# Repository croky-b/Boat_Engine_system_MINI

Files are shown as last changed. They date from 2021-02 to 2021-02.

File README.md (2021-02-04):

# Boat_Engine_system_MINI
Adaptation du projet de :https://github.com/TheDIYGuy999/Rc_Engine_Sound_ESP32 pour une utilisation "bateau"

Errata : Board Ver 1.6 : ESC1 et Led  4 partage la même Pin 19 

Il est possible de couper la piste en arriere de la resistance R10 et de relier un cable de R10 à D15 

une Nouvelle version 1.7 serra uploader

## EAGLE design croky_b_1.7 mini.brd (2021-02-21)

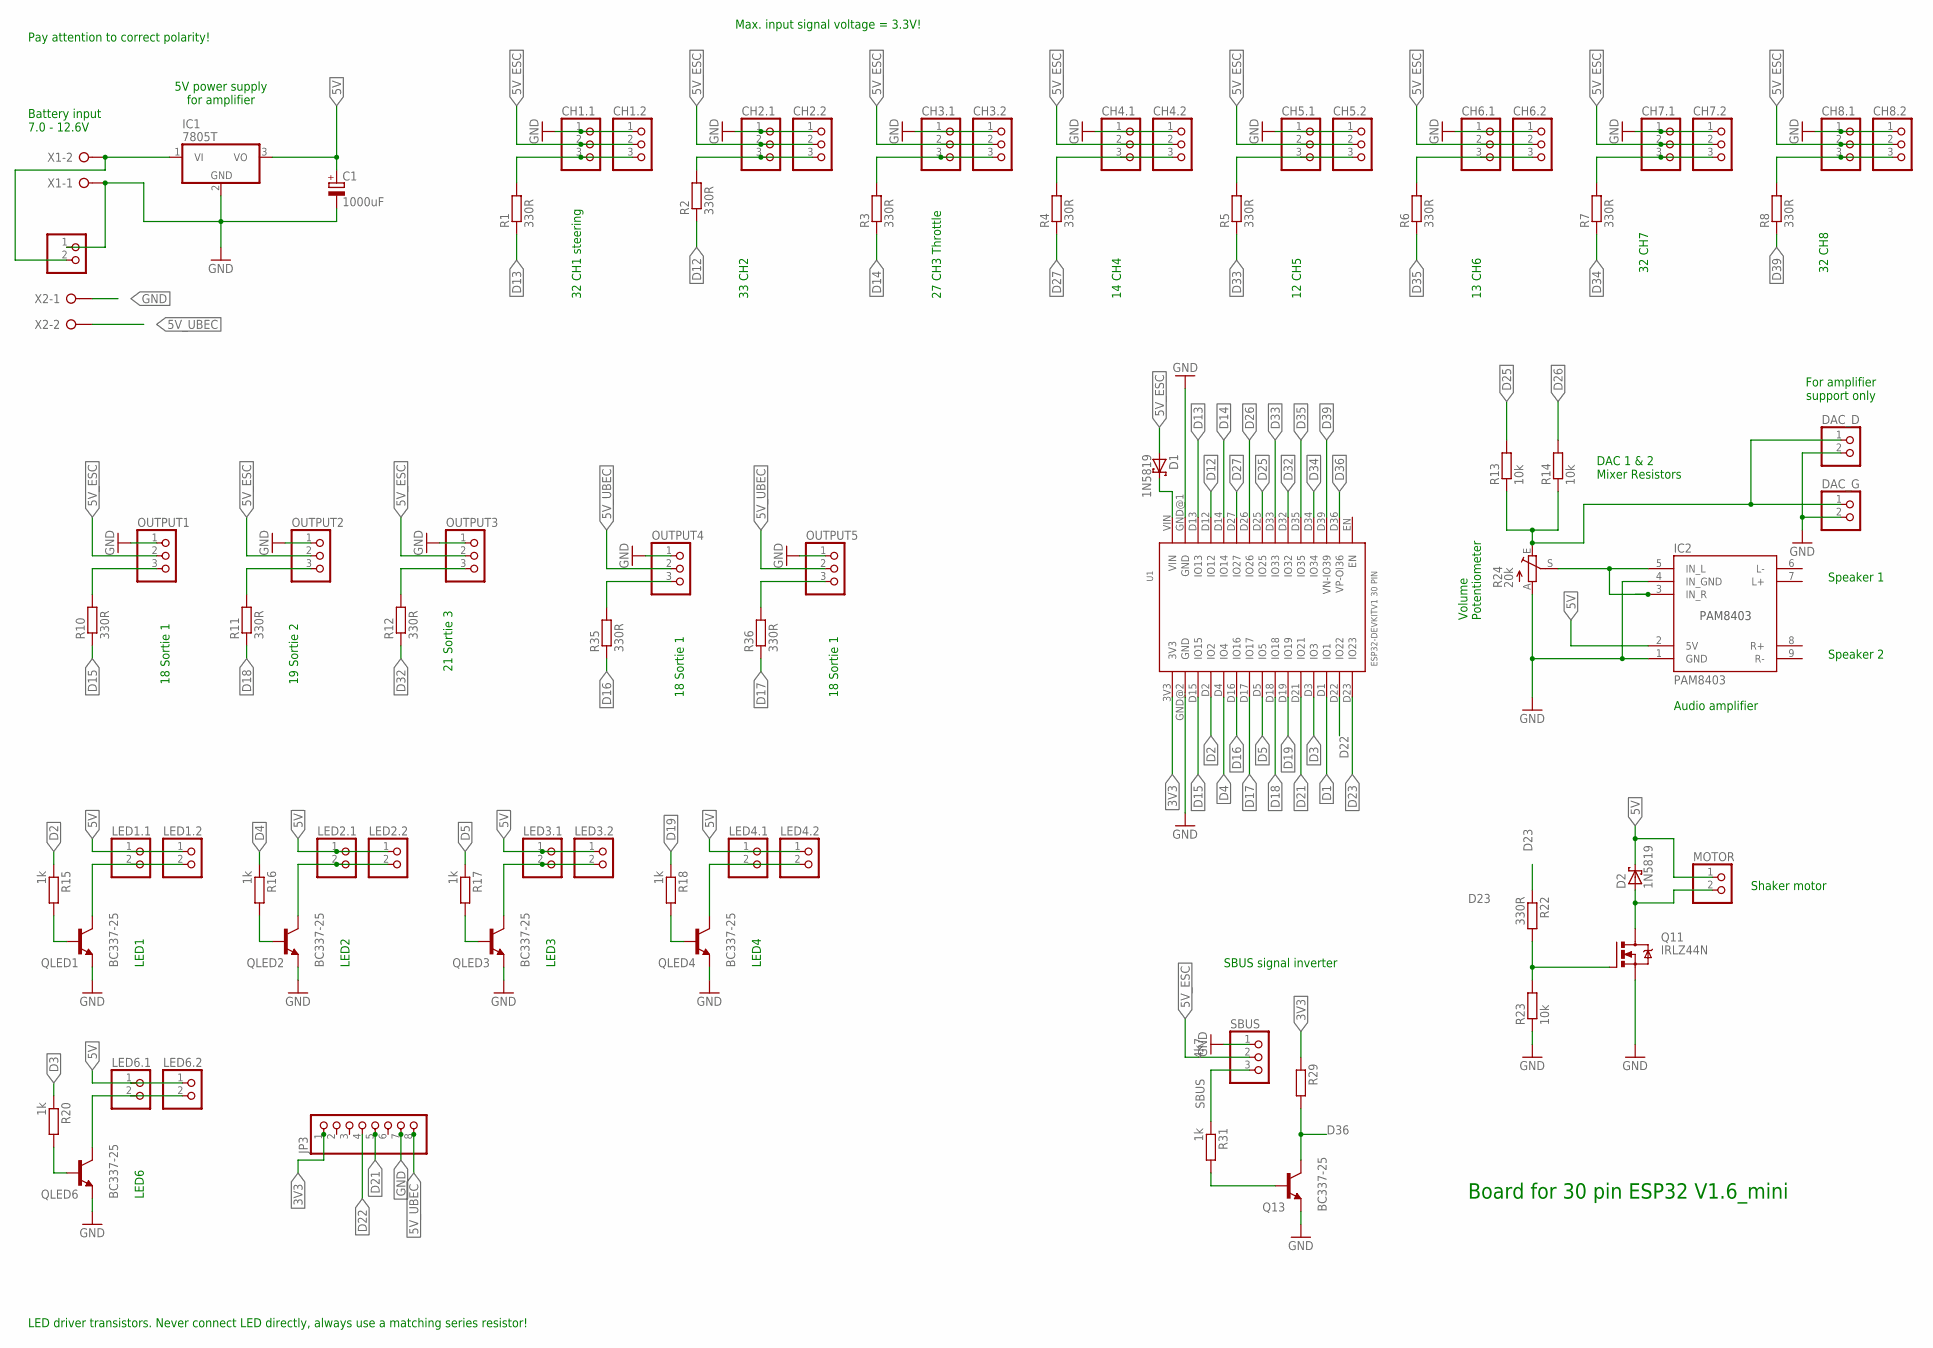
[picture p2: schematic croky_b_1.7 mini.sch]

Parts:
C1: 1000uF; E5-10,5
CH1.1, CH1.2, CH2.1, CH2.2, CH3.1, CH3.2, CH4.1, CH4.2, CH5.1, CH5.2, CH6.1, CH6.2, CH7.1, CH7.2, CH8.1, CH8.2: PINHD-1X3; 1X03
D1, D2: 1N5819; DO35-7
DAC_D: PINHD-1X2; 1X02
DAC_G: PINHD-1X2; 1X02
IC1: 7805T; TO220H
IC2: PAM8403
JP3: PINHD-1X8; 1X08
LED1.1, LED1.2, LED2.1, LED2.2, LED3.1, LED3.2, LED4.1, LED4.2, LED6.1, LED6.2: PINHD-1X2; 1X02
MOTOR, MOTOR2: PINHD-1X2; 1X02
OUTPUT1, OUTPUT2, OUTPUT3, OUTPUT4, OUTPUT5: PINHD-1X3; 1X03
Q11: IRLZ44N; TO220BV
Q13: BC337-25; TO92
QLED1, QLED2, QLED3, QLED4, QLED6: BC337-25; TO92
R1, R2, R3, R4, R5, R6, R7, R8, R10, R11, R12, R22, R35, R36: 330R; 0207/2V
R13, R14: 10k; 0207/10
R15, R16, R17, R18, R20, R31: 1k; 0207/2V
R23: 10k; 0207/2V
R24: 20k; S64W
R29: 4k7; 0207/2V
SBUS: PINHD-1X3; 1X03
U1: ESP32DEVKITV1; ESP32-DEVKITV1
X1, X2: W237-02P; W237-132

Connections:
3V3: JP3.1, R29.1, U1.3V3
5V: C1.+, D2.C, IC1.3 (VO), IC2.2 (5V), LED1.1.1, LED1.2.1, LED2.1.1, LED2.2.1, LED3.1.1, LED3.2.1, LED4.1.1, LED4.2.1, LED6.1.1, LED6.2.1, MOTOR.1
5V_ESC: CH1.1.2, CH1.2.2, CH2.1.2, CH2.2.2, CH3.1.2, CH3.2.2, CH4.1.2, CH4.2.2, CH5.1.2, CH5.2.2, CH6.1.2, CH6.2.2, CH7.1.2, CH7.2.2, CH8.1.2, CH8.2.2, D1.A, OUTPUT1.2, OUTPUT2.2, OUTPUT3.2, SBUS.2
5V_UBEC: JP3.8, OUTPUT4.2, OUTPUT5.2, X2.2
-: LED2.1.2, LED2.2.2, QLED2.3 (C)
--: LED3.1.2, LED3.2.2, QLED3.3 (C)
BAT+: IC1.1 (VI), MOTOR2.2, X1.2
D1: U1.D1 (IO1)
D2: R15.1, U1.D2 (IO2)
D3: R20.1, U1.D3 (IO3)
D4: R16.1, U1.D4 (IO4)
D5: R17.1, U1.D5 (IO5)
D12: R2.1, U1.D12 (IO12)
D13: R1.1, U1.D13 (IO13)
D14: R3.1, U1.D14 (IO14)
D15: R10.1, U1.D15 (IO15)
D16: R35.1, U1.D16 (IO16)
D17: R36.1, U1.D17 (IO17)
D18: R11.1, U1.D18 (IO18)
D19: R18.1, U1.D19 (IO19)
D21: JP3.5, U1.D21 (IO21)
D22: JP3.4, U1.D22 (IO22)
D23: R22.1, U1.D23 (IO23)
D25: R13.2, U1.D25 (IO25)
D26: R14.2, U1.D26 (IO26)
D27: R4.1, U1.D27 (IO27)
D32: R12.1, U1.D32 (IO32)
D33: R5.1, U1.D33 (IO33)
D34: R7.1, U1.D34 (IO34)
D35: R6.1, U1.D35 (IO35)
D36: Q13.3 (C), R29.2, U1.D36 (VP-OI36)
D39: R8.1, U1.D39 (VN-IO39)
GND: C1.-, CH1.1.1, CH1.2.1, CH2.1.1, CH2.2.1, CH3.1.1, CH3.2.1, CH4.1.1, CH4.2.1, CH5.1.1, CH5.2.1, CH6.1.1, CH6.2.1, CH7.1.1, CH7.2.1, CH8.1.1, CH8.2.1, DAC_D.2, DAC_G.2, IC1.2 (GND), IC2.1 (GND), IC2.4 (IN_GND), JP3.7, MOTOR2.1, OUTPUT1.1, OUTPUT2.1, OUTPUT3.1, OUTPUT4.1, OUTPUT5.1, Q11.S, Q13.1 (E), QLED1.1 (E), QLED2.1 (E), QLED3.1 (E), QLED4.1 (E), QLED6.1 (E), R23.1, R24.A, SBUS.1, U1.GND@1 (GND), U1.GND@2 (GND), X1.1, X2.1
unnamed: IC2.3 (IN_R), IC2.5 (IN_L), R24.S
unnamed: CH6.1.3, CH6.2.3, R6.2
unnamed: Q11.G, R22.2, R23.2
unnamed: CH5.1.3, CH5.2.3, R5.2
unnamed: CH4.1.3, CH4.2.3, R4.2
unnamed: CH7.1.3, CH7.2.3, R7.2
unnamed: CH3.1.3, CH3.2.3, R3.2
unnamed: D1.C, U1.VIN
unnamed: CH1.1.3, CH1.2.3, R1.2
unnamed: OUTPUT1.3, R10.2
unnamed: OUTPUT2.3, R11.2
unnamed: OUTPUT3.3, R12.2
unnamed: CH2.1.3, CH2.2.3, R2.2
unnamed: D2.A, MOTOR.2, Q11.D
unnamed: QLED1.2 (B), R15.2
unnamed: QLED6.2 (B), R20.2
unnamed: LED1.1.2, LED1.2.2, QLED1.3 (C)
unnamed: LED6.1.2, LED6.2.2, QLED6.3 (C)
unnamed: DAC_D.1, DAC_G.1, R13.1, R14.1, R24.E
unnamed: QLED3.2 (B), R17.2
unnamed: QLED2.2 (B), R16.2
unnamed: QLED4.2 (B), R18.2
unnamed: LED4.1.2, LED4.2.2, QLED4.3 (C)
unnamed: Q13.2 (B), R31.2
unnamed: CH8.1.3, CH8.2.3, R8.2
unnamed: OUTPUT4.3, R35.2
unnamed: OUTPUT5.3, R36.2
SBUS: R31.1, SBUS.3

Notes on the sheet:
Speaker 1
Speaker 2
13 CH6
12 CH5
14 CH4
27 CH3 Throttle
33 CH2
32 CH1 steering
18 Sortie 1
19 Sortie 2
21 Sortie 3
DAC 1 & 2 Mixer Resistors
Audio amplifier
Volume Potentiometer
5V power supply for amplifier
Battery input 7.0 - 12.6V
Board for 30 pin ESP32 V1.6_mini
Shaker motor
LED1
LED6
LED3
LED2
LED4
LED driver transistors. Never connect LED directly, always use a matching series resistor!
For amplifier support only
Pay attention to correct polarity!
Max. input signal voltage = 3.3V!
32 CH7
32 CH8
SBUS signal inverter

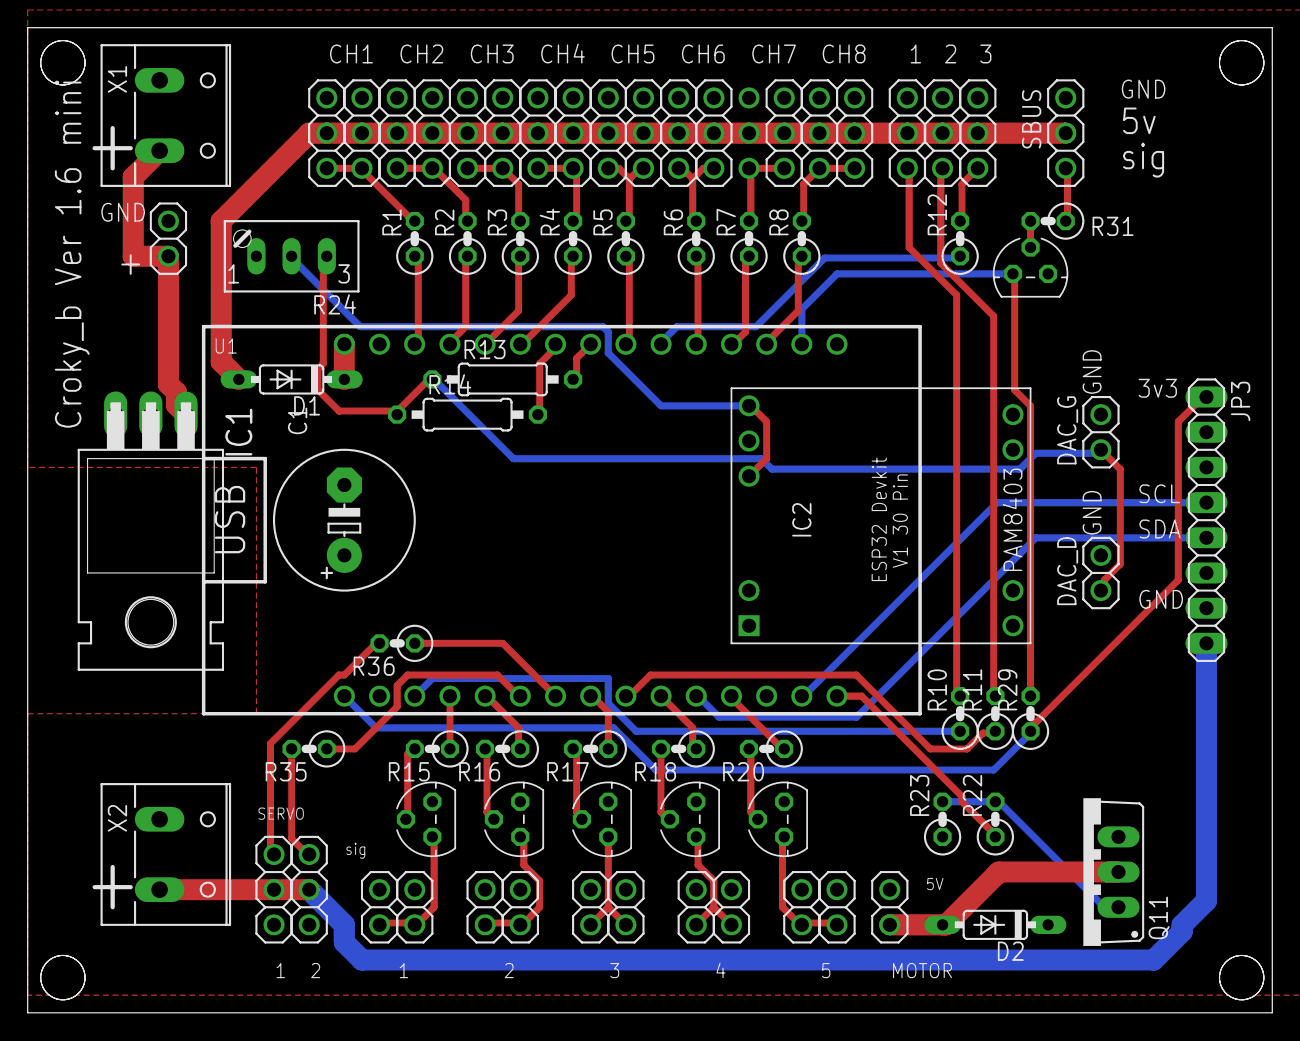
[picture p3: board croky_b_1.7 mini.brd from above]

Board: 2 copper layers, 89.8 x 71.1 mm, 77 parts (1 on the bottom side), 60 nets.

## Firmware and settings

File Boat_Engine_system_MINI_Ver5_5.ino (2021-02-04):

/* RC engine sound & LED controller for Arduino ESP32. Written by TheDIYGuy999
    Based on the code for ATmega 328: https://github.com/TheDIYGuy999/Rc_Engine_Sound
    modified for boat by croky_b for boat

 *  ***** ESP32 CPU frequency must be set to 240MHz! *****

   
*/

const float codeVersion = 5.57; // Software revision.

//
// =======================================================================================================
// SETTINGS (ADJUST THEM BEFORE CODE UPLOAD)
// =======================================================================================================
//



#include "2-Sound_config.h"
#include "1-Setup.h"
#include "driver/rmt.h"


// Make sure to remove -master from your sketch folder name

// DEBUG options can slow down the playback loop! Only comment them out for debugging
//#define PULSWIDTH_DEBUG //
//#define DEBUG // uncomment it for general debugging informations
//#define SBUS_DEBUG // uncomment it to debug the SBUS command interface on pin 36
//#define ESC_DEBUG // uncomment it to debug the ESC control

// TODO = Things to clean up!

//
// =======================================================================================================
// LIRBARIES & HEADER FILES (TABS ABOVE)
// =======================================================================================================
//

// Libraries (you have to install all of them)
#include <statusLED.h> // https://github.com/TheDIYGuy999/statusLED <<------- Install the newest version!
#include <SBUS.h>     // https://github.com/TheDIYGuy999/SBUS you need to install my fork of this library!
#include <SparkFunSX1509.h> //use my fork of this library (modified version)
#include <SlowMotionServo.h>//use my fork of this library (modified version)
#include <Servo_MCPWM.h>
#include <PWMTrigger.h>
#include "XT_DAC_Audio.h"
#include <ScheduleTable.h>

//
// =======================================================================================================
// PIN ASSIGNMENTS & GLOBAL VARIABLES (Do not play around here)
// =======================================================================================================
//
// Pin assignment and wiring instructions

// ------------------------------------------------------------------------------------
// Use a 330Ohm resistor in series with all I/O pins! allows to drive LED directly and
// provides short circuit protection.
// ------------------------------------------------------------------------------------

#define RMT_TICK_PER_US 1
// determines how many clock cycles one "tick" is
// [1..255], source is generally 80MHz APB clk
#define RMT_RX_CLK_DIV (80000000/RMT_TICK_PER_US/1000000)
// time before receiver goes idle
#define RMT_RX_MAX_US 3500

uint32_t maxPwmRpmPercentage = 400; // Limit required to prevent controller fron crashing @ high engine RPM



#define RECEIVER_CHANNELS_NUM 8
const uint8_t RECEIVER_CHANNELS[RECEIVER_CHANNELS_NUM] = {0, 1, 2, 3, 4, 5, 6, 7 };
const uint8_t RECEIVER_PINS[RECEIVER_CHANNELS_NUM]  = {13, 12, 14, 27, 33, 35, 34, 39 };


#ifdef PPM_COMMUNICATION
#define PPM_PIN    34
#endif


#ifdef SBUS_COMMUNICATION
#define COMMAND_RX  36
#define COMMAND_TX  39
#endif

#define PULSE_NBR 15

SMSSmooth monServo1;
//SMSLinear monServo1;
SMSSmooth monServo2;


Servo Servo1;
Servo Servo2;
Servo Servo3;
Servo Servo4;
Servo Servo5;
Servo Servo6;
Servo ANCHOR;
Servo ESC1;
Servo ESC2;
Servo ESC3;


PWMTrigger Action1;
PWMTrigger Action2;
PWMTrigger Action3;
PWMTrigger Action4;
PWMTrigger Action5;
PWMTrigger Action6;
PWMTrigger Action7;
PWMTrigger Action8;
PWMTrigger Action9;
PWMTrigger Action10;
PWMTrigger Action11A;
PWMTrigger Action11B;
PWMTrigger Action11C;
PWMTrigger Action11D;
PWMTrigger Action12;
PWMTrigger VolumeCh;



SchedTable<10> Sequence1Servo(SEQ1_DURATION);
SchedTable<10> Sequence1BServo(SEQ1B_DURATION);

SchedTable<2> Sequence1BLedPart1(SEQ1B_DURATION);
SchedTable<2> Sequence1BLedPart2(SEQ1B_DURATION);
SchedTable<2> Sequence1BLedPart3(SEQ1B_DURATION);
SchedTable<2> Sequence1BLedPart4(SEQ1B_DURATION);
SchedTable<2> Sequence1BSoundPart1(SEQ1B_DURATION);
SchedTable<2> Sequence1BSoundPart2(SEQ1B_DURATION);
SchedTable<2> Sequence1BSoundPart3(SEQ1B_DURATION);
SchedTable<2> Sequence1BSoundPart4(SEQ1B_DURATION);
SchedTable<2> Sequence1BMotorPart1(SEQ1B_DURATION);
SchedTable<2> Sequence1BMotorPart2(SEQ1B_DURATION);
SchedTable<2> Sequence1BMotorPart3(SEQ1B_DURATION);
SchedTable<2> Sequence1BMotorPart4(SEQ1B_DURATION);

SchedTable<2> Sequence1LedPart1(SEQ1_DURATION);
SchedTable<2> Sequence1LedPart2(SEQ1_DURATION);
SchedTable<2> Sequence1LedPart3(SEQ1_DURATION);
SchedTable<2> Sequence1LedPart4(SEQ1_DURATION);
SchedTable<2> Sequence1SoundPart1(SEQ1_DURATION);
SchedTable<2> Sequence1SoundPart2(SEQ1_DURATION);
SchedTable<2> Sequence1SoundPart3(SEQ1_DURATION);
SchedTable<2> Sequence1SoundPart4(SEQ1_DURATION);
SchedTable<2> Sequence1MotorPart1(SEQ1_DURATION);
SchedTable<2> Sequence1MotorPart2(SEQ1_DURATION);
SchedTable<2> Sequence1MotorPart3(SEQ1_DURATION);
SchedTable<2> Sequence1MotorPart4(SEQ1_DURATION);

SchedTable<10> Sequence2BServo(SEQ2B_DURATION);

SchedTable<2> Sequence2BLedPart1(SEQ2B_DURATION);
SchedTable<2> Sequence2BLedPart2(SEQ2B_DURATION);
SchedTable<2> Sequence2BLedPart3(SEQ2B_DURATION);
SchedTable<2> Sequence2BLedPart4(SEQ2B_DURATION);
SchedTable<2> Sequence2BSoundPart1(SEQ2B_DURATION);
SchedTable<2> Sequence2BSoundPart2(SEQ2B_DURATION);
SchedTable<2> Sequence2BSoundPart3(SEQ2B_DURATION);
SchedTable<2> Sequence2BSoundPart4(SEQ2B_DURATION);
SchedTable<2> Sequence2BMotorPart1(SEQ2B_DURATION);
SchedTable<2> Sequence2BMotorPart2(SEQ2B_DURATION);
SchedTable<2> Sequence2BMotorPart3(SEQ2B_DURATION);
SchedTable<2> Sequence2BMotorPart4(SEQ2B_DURATION);

SchedTable<10> Sequence2Servo(SEQ2_DURATION);

SchedTable<2> Sequence2LedPart1(SEQ2_DURATION);
SchedTable<2> Sequence2LedPart2(SEQ2_DURATION);
SchedTable<2> Sequence2LedPart3(SEQ2_DURATION);
SchedTable<2> Sequence2LedPart4(SEQ2_DURATION);
SchedTable<2> Sequence2SoundPart1(SEQ2_DURATION);
SchedTable<2> Sequence2SoundPart2(SEQ2_DURATION);
SchedTable<2> Sequence2SoundPart3(SEQ2_DURATION);
SchedTable<2> Sequence2SoundPart4(SEQ2_DURATION);
SchedTable<2> Sequence2MotorPart1(SEQ2B_DURATION);
SchedTable<2> Sequence2MotorPart2(SEQ2_DURATION);
SchedTable<2> Sequence2MotorPart3(SEQ2_DURATION);
SchedTable<2> Sequence2MotorPart4(SEQ2_DURATION);

SchedTable<10> Sequence6Servo(SEQ6_DURATION);
SchedTable<10> Sequence6BServo(SEQ6B_DURATION);


SchedTable<2> Sequence6BSoundPart1(SEQ6B_DURATION);
SchedTable<2> Sequence6BSoundPart2(SEQ6B_DURATION);
SchedTable<2> Sequence6BSoundPart3(SEQ6B_DURATION);
SchedTable<2> Sequence6BSoundPart4(SEQ6B_DURATION);



SchedTable<2> Sequence6SoundPart1(SEQ6_DURATION);
SchedTable<2> Sequence6SoundPart2(SEQ6_DURATION);
SchedTable<2> Sequence6SoundPart3(SEQ6_DURATION);
SchedTable<2> Sequence6SoundPart4(SEQ6_DURATION);

SchedTable<10> Sequence7BServo(SEQ7B_DURATION);


SchedTable<2> Sequence7BSoundPart1(SEQ7B_DURATION);
SchedTable<2> Sequence7BSoundPart2(SEQ7B_DURATION);
SchedTable<2> Sequence7BSoundPart3(SEQ7B_DURATION);
SchedTable<2> Sequence7BSoundPart4(SEQ7B_DURATION);

SchedTable<10> Sequence7Servo(SEQ7_DURATION);


SchedTable<2> Sequence7SoundPart1(SEQ7_DURATION);
SchedTable<2> Sequence7SoundPart2(SEQ7_DURATION);
SchedTable<2> Sequence7SoundPart3(SEQ7_DURATION);
SchedTable<2> Sequence7SoundPart4(SEQ7_DURATION);

PWMTrigger CH1;
PWMTrigger CH2;
PWMTrigger CH3;
PWMTrigger CH4;
PWMTrigger CH5;
PWMTrigger CH6;
PWMTrigger CH7;
PWMTrigger CH8;
PWMTrigger CH9;
PWMTrigger CH10;
PWMTrigger CH11;
PWMTrigger CH12;
PWMTrigger CH13;
PWMTrigger CH14;
PWMTrigger CH15;
PWMTrigger CH16;






// SX1509 I2C address (set by ADDR1 and ADDR0 (00 by default):
const byte SX1509_ADDRESS = 0x3E;  // SX1509 I2C address
SX1509 Led; // Create an SX1509 object to be used throughout


#define LED_PIN       2   // LED 2

#define DAC1    25 // connect pin25 (do not change the pin) to a 10kOhm resistor
XT_DAC_Audio_Class DacAudio(26, 1); // Create the main player class object. Use GPIO 25, one of the 2 DAC pins and timer 0//

// both outputs of the resistors above are connected together and then to the outer leg of a
// 10kOhm potentiometer. The other outer leg connects to GND. The middle leg connects to both inputs
// of a PAM8403 amplifier and allows to adjust the volume. This way, two speakers can be used.



// Status LED objects (also used for PWM shaker motor and ESC control)
// "false" = output not inversed

statusLED Led1(false);
statusLED Led2(false);
statusLED Led3(false);
statusLED Led4(false);
statusLED Led5(false);
statusLED Motor1(false);



volatile boolean Seq1LedPart1OnOff= false;
volatile boolean Seq1LedPart2OnOff= false;
volatile boolean Seq1LedPart3OnOff= false;
volatile boolean Seq1LedPart4OnOff= false;

volatile boolean Seq1SoundPart1OnOff = false;
volatile boolean Seq1SoundPart2OnOff = false;
volatile boolean Seq1SoundPart3OnOff = false;
volatile boolean Seq1SoundPart4OnOff = false;
volatile boolean NeutralCtl= false;
volatile boolean Test= false;



float StartServoSeq1Part1;
float EndServoSeq1Part1Mapped;
float StartServoSeq1Part1Mapped;
float DistanceServoSeq1Part1;/// P maj 
float SpeedSeq1Part1;

float StartServobSeq1Part1;
float EndServobSeq1Part1Mapped;
float StartServobSeq1Part1Mapped;
float DistanceServobSeq1Part1;/// P maj 
float SpeedbSeq1Part1;


float StartServoSeq1Part2;
float EndServoSeq1Part2Mapped;
float StartServoSeq1Part2Mapped;
float DistanceServoSeq1Part2;
float SpeedSeq1Part2;

float StartServobSeq1Part2;
float EndServobSeq1Part2Mapped;
float StartServobSeq1Part2Mapped;
float DistanceServobSeq1Part2;
float SpeedbSeq1Part2;

float StartServoSeq1Part3;
float EndServoSeq1Part3Mapped;
float StartServoSeq1Part3Mapped;
float DistanceServoSeq1Part3;
float SpeedSeq1Part3;

float StartServobSeq1Part3;
float EndServobSeq1Part3Mapped;
float StartServobSeq1Part3Mapped;
float DistanceServobSeq1Part3;
float SpeedbSeq1Part3;

float StartServoSeq1Part4;
float EndServoSeq1Part4Mapped;
float StartServoSeq1Part4Mapped;
float DistanceServoSeq1Part4;
float SpeedSeq1Part4;

float StartServobSeq1Part4;
float EndServobSeq1Part4Mapped;
float StartServobSeq1Part4Mapped;
float DistanceServobSeq1Part4;
float SpeedbSeq1Part4;

////////////////////////////////

float StartServoSeq10Part1;
float EndServoSeq10Part1Mapped;
float StartServoSeq10Part1Mapped;
float DistanceServoSeq10Part1;/// P maj 
float SpeedSeq10Part1;

float StartServobSeq10Part1;
float EndServobSeq10Part1Mapped;
float StartServobSeq10Part1Mapped;
float DistanceServobSeq10Part1;/// P maj 
float SpeedbSeq10Part1;


float StartServoSeq10Part2;
float EndServoSeq10Part2Mapped;
float StartServoSeq10Part2Mapped;
float DistanceServoSeq10Part2;
float SpeedSeq10Part2;

float StartServobSeq10Part2;
float EndServobSeq10Part2Mapped;
float StartServobSeq10Part2Mapped;
float DistanceServobSeq10Part2;
float SpeedbSeq10Part2;

float StartServoSeq10Part3;
float EndServoSeq10Part3Mapped;
float StartServoSeq10Part3Mapped;
float DistanceServoSeq10Part3;
float SpeedSeq10Part3;

float StartServobSeq10Part3;
float EndServobSeq10Part3Mapped;
float StartServobSeq10Part3Mapped;
float DistanceServobSeq10Part3;
float SpeedbSeq10Part3;

float StartServoSeq10Part4;
float EndServoSeq10Part4Mapped;
float StartServoSeq10Part4Mapped;
float DistanceServoSeq10Part4;
float SpeedSeq10Part4;

float StartServobSeq10Part4;
float EndServobSeq10Part4Mapped;
float StartServobSeq10Part4Mapped;
float DistanceServobSeq10Part4;
float SpeedbSeq10Part4;


volatile boolean Seq2LedPart1OnOff= false;
volatile boolean Seq2LedPart2OnOff= false;
volatile boolean Seq2LedPart3OnOff= false;
volatile boolean Seq2LedPart4OnOff= false;

volatile boolean Seq2SoundPart1OnOff = false;
volatile boolean Seq2SoundPart2OnOff = false;
volatile boolean Seq2SoundPart3OnOff = false;
volatile boolean Seq2SoundPart4OnOff = false;



float StartServoSeq2Part1;
float EndServoSeq2Part1Mapped;
float StartServoSeq2Part1Mapped;
float DistanceServoSeq2Part1;/// P maj 
float SpeedSeq2Part1;

float StartServobSeq2Part1;
float EndServobSeq2Part1Mapped;
float StartServobSeq2Part1Mapped;
float DistanceServobSeq2Part1;/// P maj 
float SpeedbSeq2Part1;


float StartServoSeq2Part2;
float EndServoSeq2Part2Mapped;
float StartServoSeq2Part2Mapped;
float DistanceServoSeq2Part2;
float SpeedSeq2Part2;

float StartServobSeq2Part2;
float EndServobSeq2Part2Mapped;
float StartServobSeq2Part2Mapped;
float DistanceServobSeq2Part2;
float SpeedbSeq2Part2;

float StartServoSeq2Part3;
float EndServoSeq2Part3Mapped;
float StartServoSeq2Part3Mapped;
float DistanceServoSeq2Part3;
float SpeedSeq2Part3;

float StartServobSeq2Part3;
float EndServobSeq2Part3Mapped;
float StartServobSeq2Part3Mapped;
float DistanceServobSeq2Part3;
float SpeedbSeq2Part3;

float StartServoSeq2Part4;
float EndServoSeq2Part4Mapped;
float StartServoSeq2Part4Mapped;
float DistanceServoSeq2Part4;
float SpeedSeq2Part4;

float StartServobSeq2Part4;
float EndServobSeq2Part4Mapped;
float StartServobSeq2Part4Mapped;
float DistanceServobSeq2Part4;
float SpeedbSeq2Part4;


float StartServoSeq20Part1;
float EndServoSeq20Part1Mapped;
float StartServoSeq20Part1Mapped;
float DistanceServoSeq20Part1;/// P maj 
float SpeedSeq20Part1;

float StartServobSeq20Part1;
float EndServobSeq20Part1Mapped;
float StartServobSeq20Part1Mapped;
float DistanceServobSeq20Part1;/// P maj 
float SpeedbSeq20Part1;


float StartServoSeq20Part2;
float EndServoSeq20Part2Mapped;
float StartServoSeq20Part2Mapped;
float DistanceServoSeq20Part2;
float SpeedSeq20Part2;

float StartServobSeq20Part2;
float EndServobSeq20Part2Mapped;
float StartServobSeq20Part2Mapped;
float DistanceServobSeq20Part2;
float SpeedbSeq20Part2;

float StartServoSeq20Part3;
float EndServoSeq20Part3Mapped;
float StartServoSeq20Part3Mapped;
float DistanceServoSeq20Part3;
float SpeedSeq20Part3;

float StartServobSeq20Part3;
float EndServobSeq20Part3Mapped;
float StartServobSeq20Part3Mapped;
float DistanceServobSeq20Part3;
float SpeedbSeq20Part3;

float StartServoSeq20Part4;
float EndServoSeq20Part4Mapped;
float StartServoSeq20Part4Mapped;
float DistanceServoSeq20Part4;
float SpeedSeq20Part4;

float StartServobSeq20Part4;
float EndServobSeq20Part4Mapped;
float StartServobSeq20Part4Mapped;
float DistanceServobSeq20Part4;
float SpeedbSeq20Part4;

volatile boolean Seq6LedPart1OnOff= false;
volatile boolean Seq6LedPart2OnOff= false;
volatile boolean Seq6LedPart3OnOff= false;
volatile boolean Seq6LedPart4OnOff= false;

volatile boolean Seq6SoundPart1OnOff = false;
volatile boolean Seq6SoundPart2OnOff = false;
volatile boolean Seq6SoundPart3OnOff = false;
volatile boolean Seq6SoundPart4OnOff = false;



float StartServoSeq6Part1;
float EndServoSeq6Part1Mapped;
float StartServoSeq6Part1Mapped;
float DistanceServoSeq6Part1;/// P maj 
float SpeedSeq6Part1;

float StartServobSeq6Part1;
float EndServobSeq6Part1Mapped;
float StartServobSeq6Part1Mapped;
float DistanceServobSeq6Part1;/// P maj 
float SpeedbSeq6Part1;


float StartServoSeq6Part2;
float EndServoSeq6Part2Mapped;
float StartServoSeq6Part2Mapped;
float DistanceServoSeq6Part2;
float SpeedSeq6Part2;

float StartServobSeq6Part2;
float EndServobSeq6Part2Mapped;
float StartServobSeq6Part2Mapped;
float DistanceServobSeq6Part2;
float SpeedbSeq6Part2;

float StartServoSeq6Part3;
float EndServoSeq6Part3Mapped;
float StartServoSeq6Part3Mapped;
float DistanceServoSeq6Part3;
float SpeedSeq6Part3;

float StartServobSeq6Part3;
float EndServobSeq6Part3Mapped;
float StartServobSeq6Part3Mapped;
float DistanceServobSeq6Part3;
float SpeedbSeq6Part3;

float StartServoSeq6Part4;
float EndServoSeq6Part4Mapped;
float StartServoSeq6Part4Mapped;
float DistanceServoSeq6Part4;
float SpeedSeq6Part4;

float StartServobSeq6Part4;
float EndServobSeq6Part4Mapped;
float StartServobSeq6Part4Mapped;
float DistanceServobSeq6Part4;
float SpeedbSeq6Part4;

////////////////////////////////

float StartServoSeq60Part1;
float EndServoSeq60Part1Mapped;
float StartServoSeq60Part1Mapped;
float DistanceServoSeq60Part1;/// P maj 
float SpeedSeq60Part1;

float StartServobSeq60Part1;
float EndServobSeq60Part1Mapped;
float StartServobSeq60Part1Mapped;
float DistanceServobSeq60Part1;/// P maj 
float SpeedbSeq60Part1;


float StartServoSeq60Part2;
float EndServoSeq60Part2Mapped;
float StartServoSeq60Part2Mapped;
float DistanceServoSeq60Part2;
float SpeedSeq60Part2;

float StartServobSeq60Part2;
float EndServobSeq60Part2Mapped;
float StartServobSeq60Part2Mapped;
float DistanceServobSeq60Part2;
float SpeedbSeq60Part2;

float StartServoSeq60Part3;
float EndServoSeq60Part3Mapped;
float StartServoSeq60Part3Mapped;
float DistanceServoSeq60Part3;
float SpeedSeq60Part3;

float StartServobSeq60Part3;
float EndServobSeq60Part3Mapped;
float StartServobSeq60Part3Mapped;
float DistanceServobSeq60Part3;
float SpeedbSeq60Part3;

float StartServoSeq60Part4;
float EndServoSeq60Part4Mapped;
float StartServoSeq60Part4Mapped;
float DistanceServoSeq60Part4;
float SpeedSeq60Part4;

float StartServobSeq60Part4;
float EndServobSeq60Part4Mapped;
float StartServobSeq60Part4Mapped;
float DistanceServobSeq60Part4;
float SpeedbSeq60Part4;


volatile boolean Seq7LedPart1OnOff= false;
volatile boolean Seq7LedPart2OnOff= false;
volatile boolean Seq7LedPart3OnOff= false;
volatile boolean Seq7LedPart4OnOff= false;

volatile boolean Seq7SoundPart1OnOff = false;
volatile boolean Seq7SoundPart2OnOff = false;
volatile boolean Seq7SoundPart3OnOff = false;
volatile boolean Seq7SoundPart4OnOff = false;



float StartServoSeq7Part1;
float EndServoSeq7Part1Mapped;
float StartServoSeq7Part1Mapped;
float DistanceServoSeq7Part1;/// P maj 
float SpeedSeq7Part1;

float StartServobSeq7Part1;
float EndServobSeq7Part1Mapped;
float StartServobSeq7Part1Mapped;
float DistanceServobSeq7Part1;/// P maj 
float SpeedbSeq7Part1;


float StartServoSeq7Part2;
float EndServoSeq7Part2Mapped;
float StartServoSeq7Part2Mapped;
float DistanceServoSeq7Part2;
float SpeedSeq7Part2;

float StartServobSeq7Part2;
float EndServobSeq7Part2Mapped;
float StartServobSeq7Part2Mapped;
float DistanceServobSeq7Part2;
float SpeedbSeq7Part2;

float StartServoSeq7Part3;
float EndServoSeq7Part3Mapped;
float StartServoSeq7Part3Mapped;
float DistanceServoSeq7Part3;
float SpeedSeq7Part3;

float StartServobSeq7Part3;
float EndServobSeq7Part3Mapped;
float StartServobSeq7Part3Mapped;
float DistanceServobSeq7Part3;
float SpeedbSeq7Part3;

float StartServoSeq7Part4;
float EndServoSeq7Part4Mapped;
float StartServoSeq7Part4Mapped;
float DistanceServoSeq7Part4;
float SpeedSeq7Part4;

float StartServobSeq7Part4;
float EndServobSeq7Part4Mapped;
float StartServobSeq7Part4Mapped;
float DistanceServobSeq7Part4;
float SpeedbSeq7Part4;


float StartServoSeq70Part1;
float EndServoSeq70Part1Mapped;
float StartServoSeq70Part1Mapped;
float DistanceServoSeq70Part1;/// P maj 
float SpeedSeq70Part1;

float StartServobSeq70Part1;
float EndServobSeq70Part1Mapped;
float StartServobSeq70Part1Mapped;
float DistanceServobSeq70Part1;/// P maj 
float SpeedbSeq70Part1;


float StartServoSeq70Part2;
float EndServoSeq70Part2Mapped;
float StartServoSeq70Part2Mapped;
float DistanceServoSeq70Part2;
float SpeedSeq70Part2;

float StartServobSeq70Part2;
float EndServobSeq70Part2Mapped;
float StartServobSeq70Part2Mapped;
float DistanceServobSeq70Part2;
float SpeedbSeq70Part2;

float StartServoSeq70Part3;
float EndServoSeq70Part3Mapped;
float StartServoSeq70Part3Mapped;
float DistanceServoSeq70Part3;
float SpeedSeq70Part3;

float StartServobSeq70Part3;
float EndServobSeq70Part3Mapped;
float StartServobSeq70Part3Mapped;
float DistanceServobSeq70Part3;
float SpeedbSeq70Part3;

float StartServoSeq70Part4;
float EndServoSeq70Part4Mapped;
float StartServoSeq70Part4Mapped;
float DistanceServoSeq70Part4;
float SpeedSeq70Part4;

float StartServobSeq70Part4;
float EndServobSeq70Part4Mapped;
float StartServobSeq70Part4Mapped;
float DistanceServobSeq70Part4;
float SpeedbSeq70Part4;
volatile float SERVO_START_POS[7];

double mapf(double val, double in_min, double in_max, double out_min, double out_max) {
    return (val - in_min) * (out_max - out_min) / (in_max - in_min) + out_min;
}

// Define global variables
static uint32_t curEngineSample2; 
volatile int16_t masterVolume = 100;
volatile boolean   Init = false;
volatile boolean   one = false;
volatile boolean   Setupsequence = false;

volatile boolean failSafe           = false;    // Triggered in emergency situations like: serial signal lost etc.
volatile int8_t  ppmFailsafeCounter = 0;

volatile uint8_t dacOffset = 0;  // 128, but needs to ba ramped up slowly to prevent popping noise, if switched on

volatile uint8_t engineState = 0; // 0 = off, 1 = starting, 2 = running, 3 = stopping
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
void loop()
{

#if defined SBUS_COMMUNICATION
  readSbusCommands(); // SBUS communication (pin 36)
#elif defined PPM_COMMUNICATION
  readPpmCommands(); // PPM communication (pin 34)
#else
  //  measure RC signals mark space ratio
  readRcSignals();

#endif
 
  steering();
  
  trigger();
  Servos(); 
  
  Initialisation();

  volumeControl();

  DacAudio.FillBuffer();
  Sequences();

  SlowMotionServo::update(); /* actualisation de la position */
  ScheduleTable::update();

 

}

//
// =======================================================================================================
// 1st MAIN TASK, RUNNING ON CORE 0 (Interrupts are running on this core as well)
// =======================================================================================================
//

void Task1code(void *pvParameters)
{
  for (;;)
  {
    // DAC offset fader
    dacOffsetFade();

    // Map pulsewidth to throttle
    mapThrottle();

    // Simulate engine mass, generate RPM signal
    engineMassSimulation();

    // Switch engine on or off
    engineOnOff();

    // LED control
    led();

    // Radar control
    Radar();
    
    Action();

    Motor2();

    // ESC control
    esc();

    triggerSound();
   


  }
}

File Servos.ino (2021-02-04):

//
// =======================================================================================================
// 													SERVOS
// =======================================================================================================
//

void Servos()

{

//if (Init) {


    static unsigned long lastStateTime;

     if (millis() - lastStateTime > 300)     // Print the data every 300ms
      {
        lastStateTime = millis();

        Serial.println(CH4.momentaryPos());
        
        
      }



 

    #ifdef ACTION2_ENABLE
     #ifdef ANCHORMOTOR

        #ifdef ANCHORMOTOR_1
    if (Mouillage && !AncreBas) {
      
      Servo1.writeMicroseconds(AnchorSpeedDown);
    } else if (!Mouillage && AncreBas) {
      Servo1.writeMicroseconds(AnchorSpeedUp);
    }

    if (AncreStop) {

      Servo1.writeMicroseconds(1500);
      AnchorSpeedDown = 1600;
      AnchorSpeedUp = 1400;
    }
        #endif
        
      #ifdef ANCHORMOTOR_2
    if (Mouillage && !AncreBas) {
      
      Servo2.writeMicroseconds(AnchorSpeedDown);
    } else if (!Mouillage && AncreBas) {
      Servo2.writeMicroseconds(AnchorSpeedUp);
    }

    if (AncreStop) {

      Servo2.writeMicroseconds(1500);
      AnchorSpeedDown = 1600;
      AnchorSpeedUp = 1400;
    }
        #endif 

       #ifdef ANCHORMOTOR_3
    if (Mouillage && !AncreBas) {
      
      Servo3.writeMicroseconds(AnchorSpeedDown);
    } else if (!Mouillage && AncreBas) {
      Servo3.writeMicroseconds(AnchorSpeedUp);
    }

    if (AncreStop) {

      Servo3.writeMicroseconds(1500);
      AnchorSpeedDown = 1600;
      AnchorSpeedUp = 1400;
    }
        #endif 

         #ifdef ANCHORMOTOR_4
    if (Mouillage && !AncreBas) {
      
      Servo4.writeMicroseconds(AnchorSpeedDown);
    } else if (!Mouillage && AncreBas) {
      Servo4.writeMicroseconds(AnchorSpeedUp);
    }

    if (AncreStop) {

      Servo4.writeMicroseconds(1500);
      AnchorSpeedDown = 1600;
      AnchorSpeedUp = 1400;
    }
        #endif 

       #ifdef ANCHORMOTOR_5
    if (Mouillage && !AncreBas) {
      
      Servo5.writeMicroseconds(AnchorSpeedDown);
    } else if (!Mouillage && AncreBas) {
      Servo5.writeMicroseconds(AnchorSpeedUp);
    }

    if (AncreStop) {

      Servo5.writeMicroseconds(1500);
      AnchorSpeedDown = 1600;
      AnchorSpeedUp = 1400;
    }
        #endif 
         #ifdef ANCHORMOTOR_6
    if (Mouillage && !AncreBas) {
      
      Servo6.writeMicroseconds(AnchorSpeedDown);
    } else if (!Mouillage && AncreBas) {
      Servo6.writeMicroseconds(AnchorSpeedUp);
    }

    if (AncreStop) {

      Servo6.writeMicroseconds(1500);
      AnchorSpeedDown = ANCOR_SPEED_DOWN;
      AnchorSpeedUp = ANCOR_SPEED_UP;
    }
        #endif           
    
      #endif 
    #endif

   

  
	
#ifdef ACTION12_ENABLE

  #ifdef ACT12SERVOSWITCH

    if ((!engineOn && !manualServo &&!servoHome)) {
     
    #ifdef SERVO1_HOME
        if (servoPulse[1]<SERVO_START[1]){
          
          if (millis() - servoTime[1] > 10) {
            servoTime[1] = millis();
            servoPulse[1] += servoStep;
            if (servoPulse[1] > SERVO_START[1])
              servoPulse[1] = SERVO_START[1];
          }
        }
      
      
         else if (servoPulse[1]>SERVO_START[1]){
          
          if (millis() - servoTime[1] > 10) {
            servoTime[1] = millis();
            servoPulse[1] -= servoStep;
            if (servoPulse[1] < SERVO_START[1])
              servoPulse[1] = SERVO_START[1];
          }
        } 

        #endif 

        #ifdef SERVO2_HOME

        if (servoPulse[2]<SERVO_START[2]){
          
          if (millis() - servoTime[2] > 10) {
            servoTime[2] = millis();
            servoPulse[2] += servoStep;
            if (servoPulse[2] > SERVO_START[2])
              servoPulse[2] = SERVO_START[2];
          }
        }
      
      
         else if (servoPulse[2]>SERVO_START[2]){
          
          if (millis() - servoTime[2] > 10) {
            servoTime[2] = millis();
            servoPulse[2] -= servoStep;
            if (servoPulse[2] < SERVO_START[2])
              servoPulse[2] = SERVO_START[2];
          }
        } 

        #endif

        #ifdef SERVO3_HOME

        if (servoPulse[3]<SERVO_START[3]){
          
          if (millis() - servoTime[3] > 10) {
            servoTime[3] = millis();
            servoPulse[3] += servoStep;
            if (servoPulse[3] > SERVO_START[3])
              servoPulse[3] = SERVO_START[3];
          }
        }
      
      
         else if (servoPulse[3]>SERVO_START[3]){
          
          if (millis() - servoTime[3] > 10) {
            servoTime[3] = millis();
            servoPulse[3] -= servoStep;
            if (servoPulse[3] < SERVO_START[3])
              servoPulse[3] = SERVO_START[3];
          }
        } 

        #endif 
        #ifdef SERVO4_HOME

        if (servoPulse[4]<SERVO_START[4]){
          
          if (millis() - servoTime[4] > 10) {
            servoTime[4] = millis();
            servoPulse[4] += servoStep;
            if (servoPulse[4] > SERVO_START[4])
              servoPulse[4] = SERVO_START[4];
          }
        }
      
      
         else if (servoPulse[4]>SERVO_START[4]){
          
          if (millis() - servoTime[4] > 10) {
            servoTime[4] = millis();
            servoPulse[4] -= servoStep;
            if (servoPulse[4] < SERVO_START[4])
              servoPulse[4] = SERVO_START[4];
          }
        } 

        #endif
        #ifdef SERVO5_HOME

        if (servoPulse[5]<SERVO_START[5]){
          
          if (millis() - servoTime[5] > 10) {
            servoTime[5] = millis();
            servoPulse[5] += servoStep;
            if (servoPulse[5] > SERVO_START[5])
              servoPulse[5] = SERVO_START[5];
          }
        }
      
      
         else if (servoPulse[5]>SERVO_START[5]){
          
          if (millis() - servoTime[5] > 10) {
            servoTime[5] = millis();
            servoPulse[5] -= servoStep;
            if (servoPulse[5] < SERVO_START[5])
              servoPulse[5] = SERVO_START[5];
          }
        }

        #endif

        #ifdef SERVO6_HOME

        if (servoPulse[6]<SERVO_START[6]){
          
          if (millis() - servoTime[6] > 10) {
            servoTime[6] = millis();
            servoPulse[6] += servoStep;
            if (servoPulse[6] > SERVO_START[6])
              servoPulse[6] = SERVO_START[6];
          }
        }
      
      
         else if (servoPulse[6]>SERVO_START[6]){
          
          if (millis() - servoTime[6] > 10) {
            servoTime[6] = millis();
            servoPulse[6] -= servoStep;
            if (servoPulse[6] < SERVO_START[6])
              servoPulse[6] = SERVO_START[6];
          }
        } 

        #endif
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

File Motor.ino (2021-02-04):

//
// =======================================================================================================
// RADAR : Led11 = 5v_UBEC  Led10 = 5V
// =======================================================================================================
//


void Radar()
{
  if (MotorOn)
  {
    Led.On(11);
    Motor1.on();
  }
  else
  {
    Led.Off(11);
    Motor1.off();
  }
}

//
// =======================================================================================================
// MOTOR2 Led10 = 5v_UBEC  Led10 = 5V
// =======================================================================================================
//

void Motor2()
{
    
}


//
// =======================================================================================================
// MOTOR3
// =======================================================================================================
//
void Motor3()
{

}
